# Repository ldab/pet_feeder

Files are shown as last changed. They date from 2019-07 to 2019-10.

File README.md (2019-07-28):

# Pet-Feeder
ESP8266 based Pet Feeder.








* This was more than a weekend project, took few designs to get it working, below few examples, being the last one the most successful one:

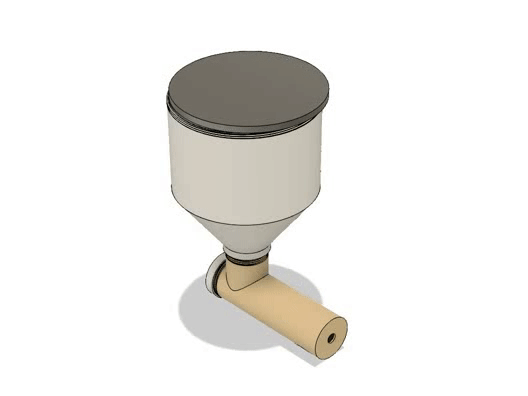
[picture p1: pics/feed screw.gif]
 

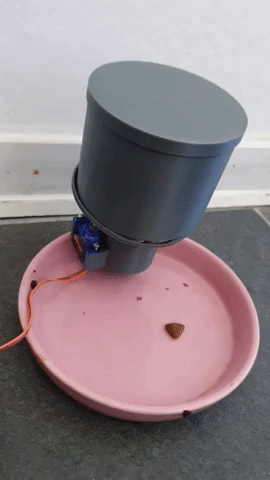
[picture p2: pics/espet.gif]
 

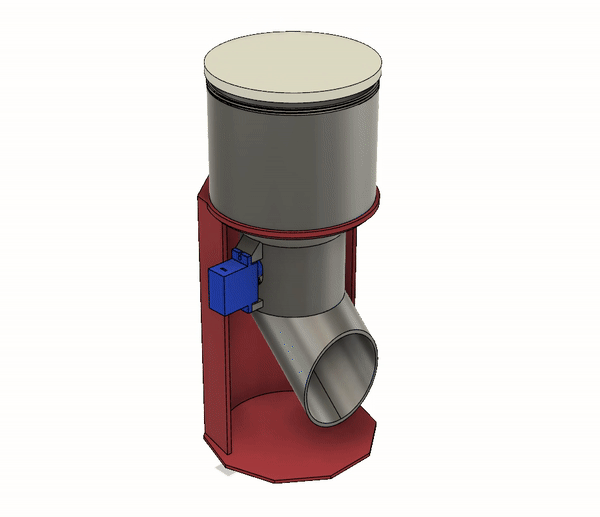
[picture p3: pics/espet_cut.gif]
 

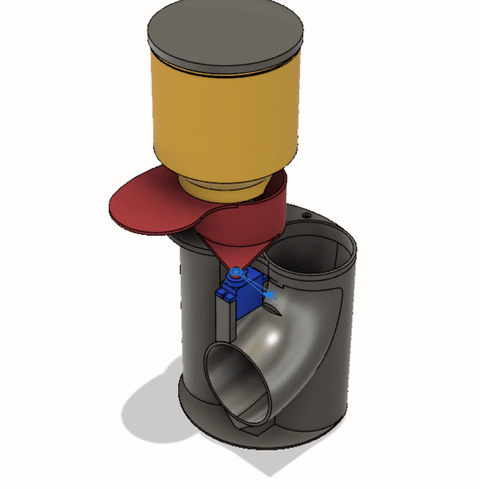
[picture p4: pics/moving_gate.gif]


## Sumary

1. [PlatformIO](/README.md#PlatformIO)
2. [Hardware](/README.md#Hardware)
3. [Blynk](/README.md#Blynk)
4. [3D Printing](/README.md#3d-printing)
5. [Credits](/README.md#Credits)

## PlatformIO

* More information can be found on their comprehensive [Docs](https://docs.platformio.org/en/latest/ide/vscode.html). But Basically:

  0. Download and install official Microsoft Visual Studio Code. PlatformIO IDE is built on top of it
  1. **Open** VSCode Package Manager
  2. **Search** for official `platformio-ide` [extension](https://marketplace.visualstudio.com/items?itemName=platformio.platformio-ide)
  3. **Install** PlatformIO IDE.

PlatformIO installation

## Hardware

### Servo

* Just using the cheap blue [SG90](https://www.google.com/search?client=firefox-b-d&q=sg90+servo):

SG90

### Board Pinout



## Blynk App

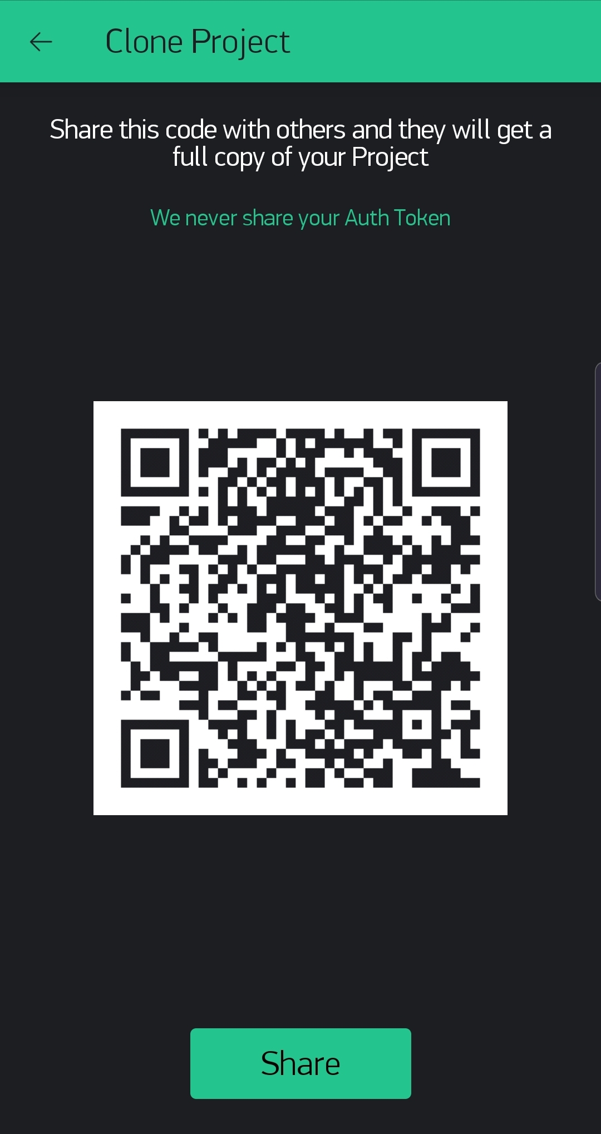
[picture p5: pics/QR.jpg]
  

## 3D Printing

* You can find the 3D files [here](./3d%20files) or [https://www.thingiverse.com/thing:3776532](https://www.thingiverse.com/thing:3776532)

* Print seetings:
  * Anycubic I3 Mega;
  * PLA 195degC;
  * 0.25 resolution;
  * No support, (only the `gate` requires it);
  * 3 walls;
  * 20% Zigzag infill;

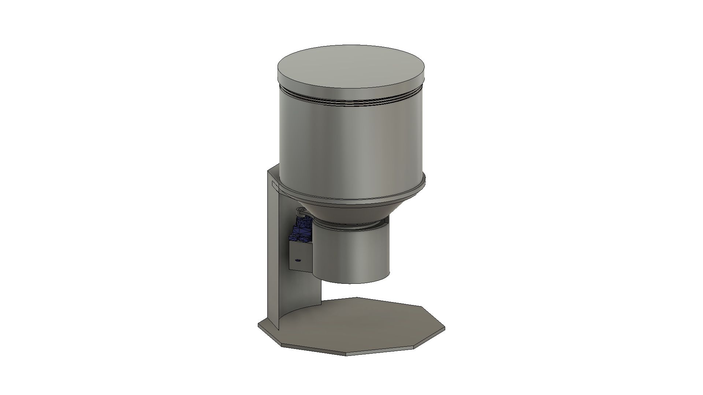
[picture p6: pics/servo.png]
 ESPet

## Credits

*.gif created with [EZGIF.COM](https://ezgif.com/)

GitHub Shields and Badges created with [Shields.io](https://github.com/badges/shields/)

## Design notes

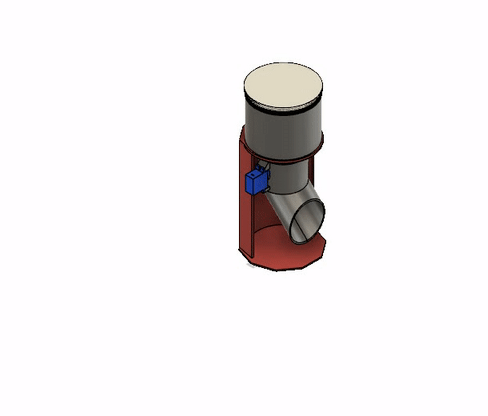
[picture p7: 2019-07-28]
pics/rotary.gif

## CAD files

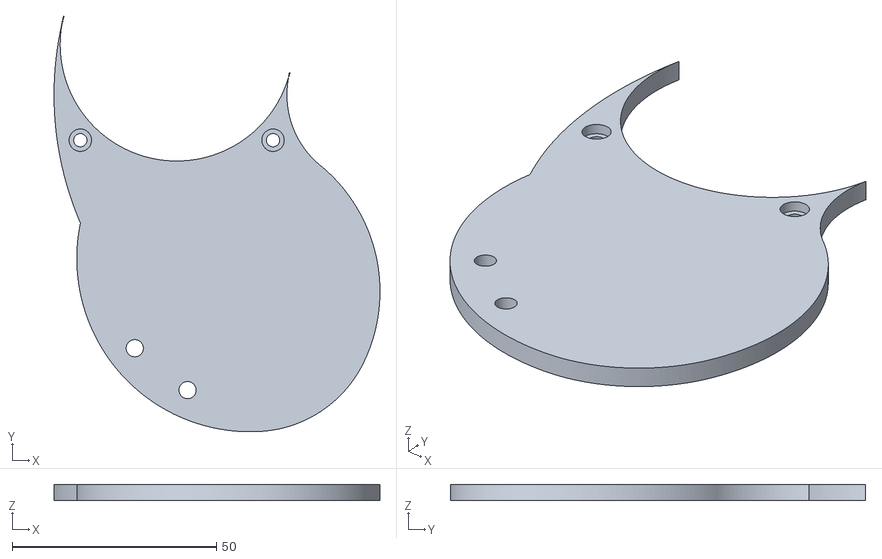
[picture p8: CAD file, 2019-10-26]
3D Files/top_base.stl
79.8 x 101.7 x 4.00

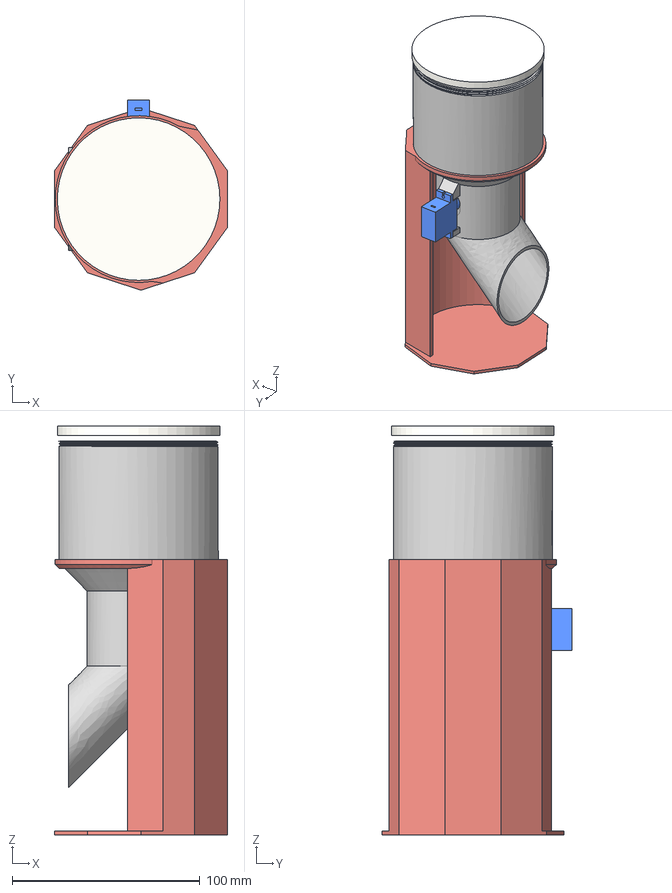
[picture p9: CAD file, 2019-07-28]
3D Files/rotating shaft v3.step
92.3 x 101.4 x 217.9 mm
Container
shaft
Lid
Base
Servo-sg90-final

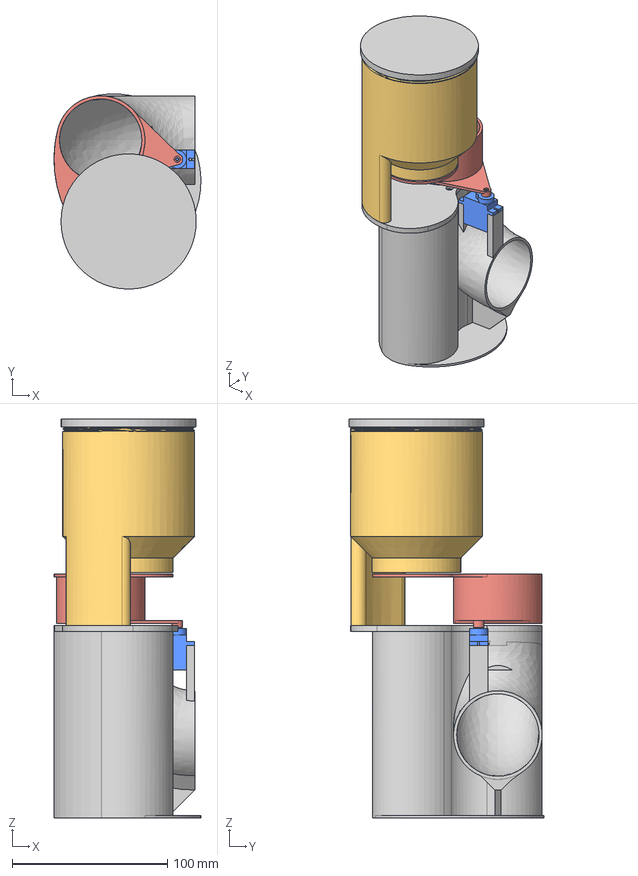
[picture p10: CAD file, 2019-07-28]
3D Files/moving_gate.step
94.5 x 125.6 x 256.8 mm
Container
Servo-sg90-final
Lid
Gate
Base

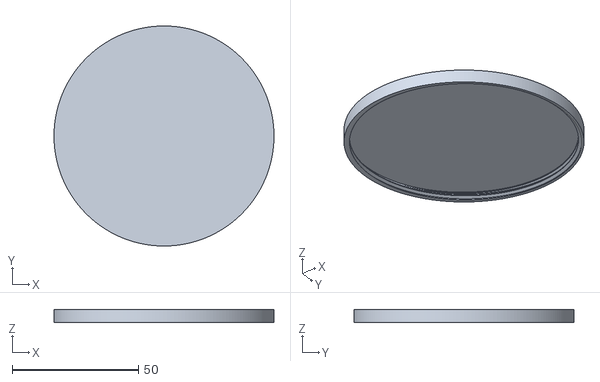
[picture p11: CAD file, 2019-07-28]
3D Files/lid.stl
87.0 x 87.0 x 5.00

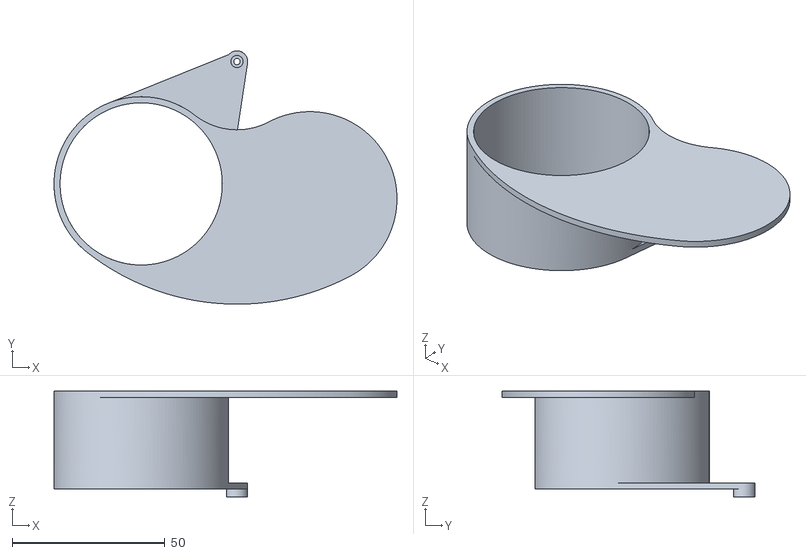
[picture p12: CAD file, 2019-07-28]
3D Files/gate.stl
112.1 x 82.8 x 34.5

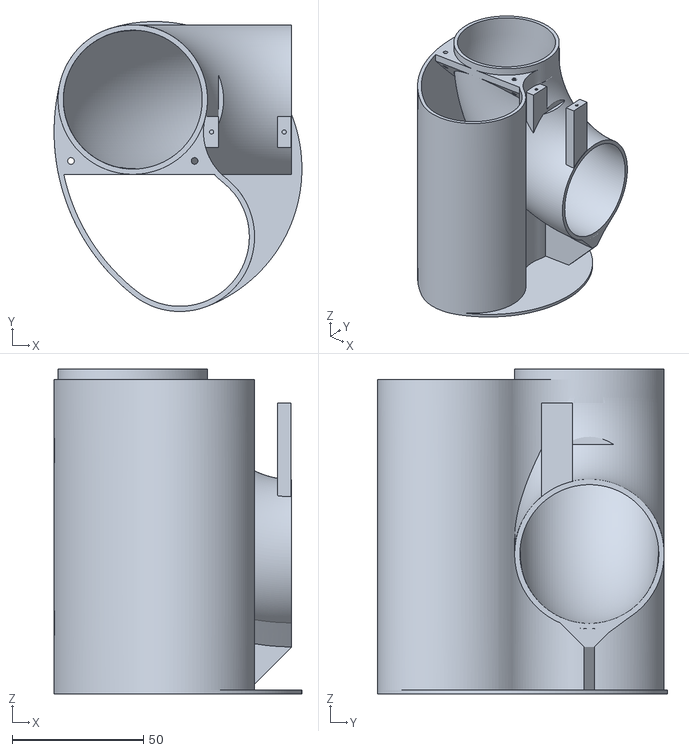
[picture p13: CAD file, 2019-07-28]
3D Files/base.stl
94.6 x 110.6 x 124.0

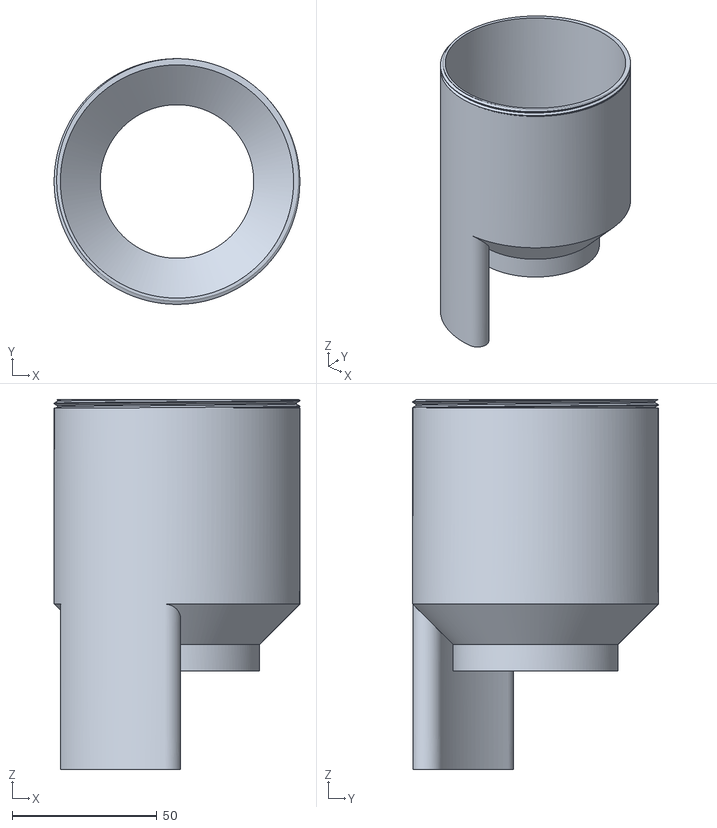
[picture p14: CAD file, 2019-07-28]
3D Files/container.stl
84.8 x 84.8 x 127.8

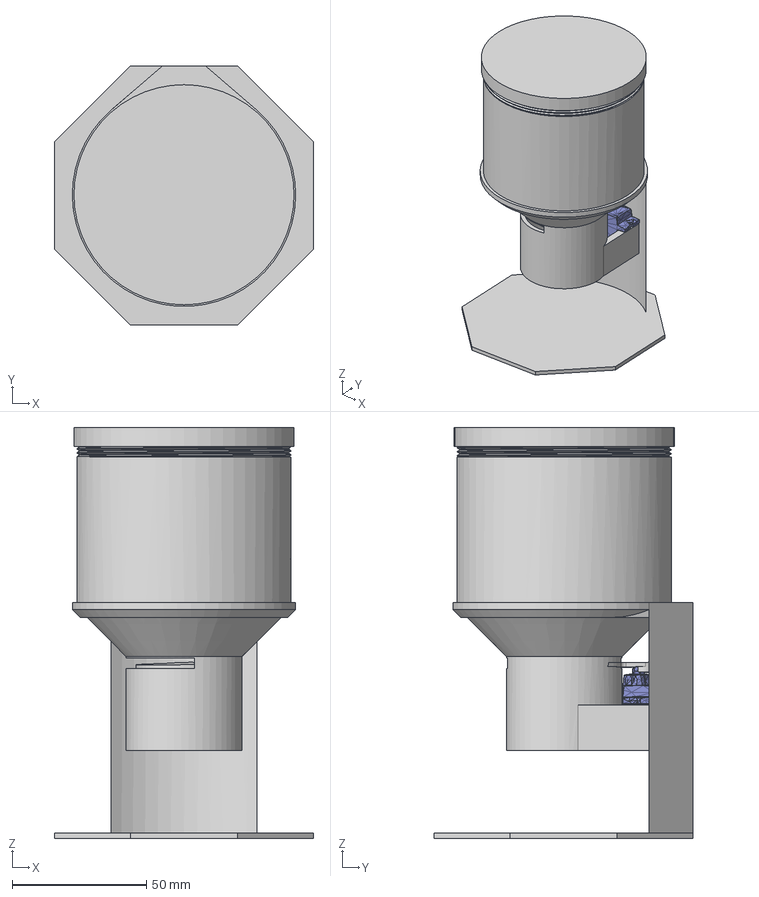
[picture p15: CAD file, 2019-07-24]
3D Files/servo v8.step
96.6 x 96.6 x 153.1 mm
Container
Lid
2051_servo_tower-pro-sg90.pk2
gate
stand

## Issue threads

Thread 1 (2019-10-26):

missing tob_base.stl in 3D Files

joelmnz, 2019-10-26:
Hi, thanks for all the great design work, just printed all parts but found the top_base.stl was missing, had to grab from thingiverse

ldab, 2019-10-26:
Thanks.

68bca5f902e01a598bd5755138487e0a18bbf724

Closed 2019-10-26.

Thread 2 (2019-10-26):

Mod to fit servo with cable

joelmnz, 2019-10-26:
Hi, appreciate the good design, as a suggestion, the servo motors that have cables on the side dont fit in the holder, my mount snapped when I tried to fit it in.

Maybe have a cut out on the servo mount close to the body for the cable to go through into the inside so we can mount the electronics inside.

If I get enough time will send through a Pull Request.

Thanks

ldab, 2019-10-26:
Thanks for the comments. I will leave this issue open so we can track it.

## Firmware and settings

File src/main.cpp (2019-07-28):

/******************************************************************************
ESP8266 based Pet Feeder
Leonardo Bispo
July - 2019
https://github.com/ldab/Pet-Feeder
Distributed as-is; no warranty is given.
******************************************************************************/
#include "Arduino.h"

/* Comment this out to disable prints and save space */
//#define BLYNK_DEBUG
#define BLYNK_PRINT Serial
#define BLYNK_NO_BUILTIN
#define BLYNK_NO_FLOAT

// Enable Debug interface and serial prints over UART1
#define DEGUB_ESP

#include <ESP8266WiFi.h>
#include <BlynkSimpleEsp8266.h>
#include <TimeLib.h>
#include <WidgetRTC.h>
#include <Servo.h>

//OTA stuff
#include <ESP8266mDNS.h>
#include <WiFiUdp.h>
#include <ArduinoOTA.h>

#ifdef DEGUB_ESP
  #define DBG(x) Serial.println(x)
#else 
  #define DBG(...)
#endif

//Servo attached to GPIO2 -> D4
//#define SERVO_PIN   2
#define SERVO_PIN   5     // D1 -> GPIO5
#define SERVO_CLOSE 90
#define SERVO_OPEN  18

int SERVO_SPEED = 50;

// WiFi and Blynk App credentials;
char ssid[] = "";
char pass[] = "";
char auth[] = "";

time_t  foodtime = -1;
bool    s_feed   = false;

uint8_t servoTimer;
uint8_t myPos = SERVO_CLOSE;

WidgetRTC  rtc;
Servo      myservo;                        // create servo object to control a servo
BlynkTimer timer;

void openServo();
void closeServo();


void feed_now()
{
  DBG( "Done feeding, closing" );

  myservo.write( SERVO_CLOSE );

  Blynk.notify("Done feeding");
}

BLYNK_CONNECTED()
{
  // Syncronize RTC when connects
  rtc.begin();
  Blynk.syncVirtual(V1);
}

BLYNK_WRITE(V1)
{
  // Simple time input, returns the time for a day in sec -> max 86400
  foodtime = param[0].asLong();

  DBG("time from app:" + String(foodtime));

  // When no input App returns 0, and -1 reset time input;
  s_feed = (foodtime > 0) ? true : false;
}

void setup()
{
  #ifdef DEGUB_ESP
    Serial.begin(19200);
  #endif

  myservo.attach( SERVO_PIN );
  //myservo.write( SERVO_CLOSE );

  Blynk.begin(auth, ssid, pass);
  rtc.begin();

  Serial.print ("SDK:");
  DBG (ESP.getSdkVersion());
  Serial.print ("Flash Chip size:");
  DBG (ESP.getFlashChipSize());
  Serial.print ("Sketch size:");
  DBG (ESP.getSketchSize());
  Serial.print ("Free sketch space:");
  DBG (ESP.getFreeSketchSpace());
  Serial.print ("Free Heap:");
  DBG (ESP.getFreeHeap());
  Serial.print ("Reset Reason:");
  DBG (ESP.getResetReason());

  ArduinoOTA.setHostname("myesp8266");
  ArduinoOTA.begin();
}

void loop()
{
  ArduinoOTA.handle();
  timer.run();
  Blynk.run();

  // Make sure time is sync before comparing
  time_t now_s = ( timeStatus() != 2 ) ? -1 : hour() * 3600 + minute() * 60 + second();

  if( now_s > foodtime && s_feed )
  {
    // Reset time input on the App
    char tz[] = "Europe/Copenhagen";
    Blynk.virtualWrite(V1, -1, -1, tz);

    // Reset flags
    foodtime = -1;
    s_feed = false;

    DBG("Feeding, open servo");

    servoTimer = timer.setInterval(SERVO_SPEED, openServo);
  }
}   //end loop

void openServo()
{
  myservo.write( myPos );

  myPos--;

  if( myPos <= SERVO_OPEN )
  {
    timer.deleteTimer(servoTimer);

    delay( 500 );

    servoTimer = timer.setInterval(SERVO_SPEED, closeServo);
  }
}

void closeServo()
{
  myservo.write( myPos );

  myPos++;

  // delete timer when reach position
  if( myPos >= SERVO_CLOSE )  timer.deleteTimer(servoTimer);
}

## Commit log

2019-07-24 v1 #fail
    [servo v8.step]
2019-07-28 new 3d model
    [base.stl, container.stl, gate.stl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]
2019-10-26 Add files via upload
    https://github.com/ldab/pet_feeder/issues/1
    [top_base.stl]

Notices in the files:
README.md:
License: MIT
